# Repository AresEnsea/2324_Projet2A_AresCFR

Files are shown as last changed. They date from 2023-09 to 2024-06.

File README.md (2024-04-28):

# 2324_Projet2A_AresCFR
## Introduction

Ce repository GitHub regroupe l'ensemble des projets & documents réalisés par l'association Ares pour la Coupe de France de Robotique 2024.

## 26/09/2023: Idées pour résoudre le problème mécanique 
### I. Partie mécanique : 

Des recherches sur internet nous on fait découvrir le Robot Trooper. 
Le site suivant permet de connaître ce robot : https://www.sick.com/fr/fr/sick-sensor-blog/trooper-le-robot-de-manutention-autonome-pour-le-distancage-en-horticulture-/w/blog-instar-robotics-success-story/

Ce deuxième site permet d'étudier la mécanique de celui-ci grâce à un concours CPGE : https://www.upsti.fr/espace-etudiants/annales-de-concours/topics/s2i-robot-trooper

Les méthodes utilisées par le robot Trooper sont:

* La récupération de pots et de cache-pots grâce à des “mains plates”. 
* Le stockage des pots grâce à un arc de cercle.

<center>

My Remote Image

Figure 1 - Robot Trooper

</center>

## 03/10/2023: 
### II. Utilisation de capteurs de fin de course :

Idées : Positionner un capteur sur chaque côté du robot afin que le contact avec une des parois de la table permette de réinitialiser l'odométrie du robot. Par dessus, positionner une pièce imprimée en 3D pour couvrir la surface totale de chaque côté à l'instar des robots aspirateurs.  

<center>

aspirateur_robotique

Figure 2 - Robot Asprirateur

</center>

### III. Utilisation de capteurs TOF [Time Of Flight] :

La différence entre un capteur classique et un capteur TOF est l'état actif et passif. Le capteur classique est passif, il se comporte "comme la rétine d'un oeil". Cependant, un capteur TOF est un composant actif car il mesure un genre "d'écho" de la lumière qu'il émet (il ne mesure donc pas la lumière ambiante).
Le principe de fonctionnement de ce capteur est de mesurer le temps que met la lumière à revenir au capteur. Cela permet notamment de déterminer sa distance par rapport aux objets environnants. 

<center>



Figure 3 - Capteur TOF : Fonctionnement 
</center>

### IV. Idées de résolution du problème mécanique :

<center>

385482582_334418605664017_5041229388081065512_n

Figure 4 - Schéma explicatif de la solution mécanique 

</center>

<center>



Figure 5 - Modélisation 3D des pots à soulever (présence d'une bordure au sommet du pot) 

</center>

<center>



Figure 6 - Modélisation 3D des plantes à soulever (ne présente pas de bordure)

</center>

1) La base du robot : en forme d'entonnoir pour guider les plantes et leurs pots jusqu'à l'endroit où se situe la première pince.
2) Un ascensceur à pots : À l'endroit où l'entonnoir a le plus petit diamètre, une première pince se charge de monter les pots dans l'esapace de stockage.
3) Un espace de stockage intégré au robot : une plateforme comporte plusieurs encoches afin d'accueillir les pots.
4) Différenciation entre les pots et les plantes fragiles et résistantes : Utilisation d'un capteur de couleur pour détecter la couleur des plantes et ainsi déterminer s'il s'agit d'une plante fragile ou non. Pour détecter si le contenant stocké est un pot ou une plante, 2 capteurs de proximité seront placées à 2 hauteurs différentes : le capteur en position haute détectera les plantes et celui du bas les pots. Nous voudrions donc utiliser un capteur RFID (RFID-RC522) en haut de l'ascenseur pour savoir si c'est un pot ou une plante qui est monté par la pince. Il faut donc récupérer en premier des pots pour les stocker puis récupérer des plantes afin de les poser directement dans les pots.
5) Descente des pots contenant les plantes : Une deuxième pince est située à l'arrière du robot, elle est composée de deux plaques qui se serrent autour du pot afin de les descendre de l'espace de stockage et de les déposer sur la table. 

### IV. Servomoteur ou moteur :

Les servomoteurs respectent avec précision une position angulaire donnée. Ils ont une rotation souvent limitée à 180° et ne tournent pas en permanence alors qu'à l'inverse, les moteurs ont un mouvement continu. Les servomoteurs seront donc très utiles pour le déplacement d'un bras robotisé.

## 10/10/2023

### V. Décisions liées à la partie mécanique:

 - Dans les 6 zones de stockage deux caches-pots sont empilés. Puisque nous ne savons pas si le cache-pot sera en métal ou en impression 3D, nous choisisons de palier ce problème en adoptant la méthode suivante : dépose d'une plante dans les deux caches-pots empilés et placement dans les jardinières (comptera pour 1 point).
   
 - Première idée de stratégie pour ramasser les pots : Notre but est de récupérer des caches-pots et d'en avoir toujours en stock. Nous voulons ensuite mettre les plantes dans les caches-pots déjà stockés. Par ailleurs, si nous n'avons plus la possibilité de récupérer des caches-pots alors quelques emplacements auront un diamètre adapté à ceux des plantes fragiles. Lorsqu'il n'y aura plus de caches-pots à récupérer, nous utiliserons un capteur de couleur pour détecter si le robot prend une plante fragile ou une plante résitsante. Si la plantes est résistante alors la base du robot la poussera jusqu'à la zone de dépose des plantes. Si la plante est fragile alors elle sera stocké dans les emplacements adaptés situés dans le stockage avant de les déposer dans les jardinières.
   
 - Idée finale de stratégie pour ramasser les pots: Chaque cache-pot et chaque plante, de n'importe quel type, sera ramassé par la pince liée à l'ascenseur. Le système vérifiera quel type d'objet est encerclé par la pince. Pour chaque montée d'objet, un capteur détermine si c'est un cache-pot ou une plante (résistante ou fragile). Si c'est un cache-pot, alors il est dircetement déposé dans l'espace de stockage s'il reste un emplacement vide. Si c'est une plante fragile, alors elle est déposée dans un emplacement qui contient déjà un pot. Si c'est une plante résistante, alors elle est déposée dans un emplacement vide si c'est possible, sinon elle est déposée dans un emplacement contenant un pot.
   
 - Résolution de l'éclairement des panneaux solaires: Positionnement de deux crémaillères sur le côté du robot afin d'appuyer sur le côté du panneau solaire pour le faire tourner d'un quart de tour.
   
 -  Dépot des plantes avec leurs caches-pots dans les jardinières : Une pince est située à l'arrière du robot. À l'endroit où les pots peuvent sortir de l'espace de stockage, nous plaçons une plaque en bois posée sur des rails qui avance et recule selon une direction. Les dimensions de la plaque en bois sont : $75mm \times 75mm \times 6mm$. De plus, nous plaçons une pince à 75 mm de distance de l'espace de stockage. Celle-ci va pouvoir récupérer les pots grâce à la plaque de bois qui avance.

## 17/10/2023

### VI. Informations concernant les actionneurs 

#### VI.a Servomoteur Dynamixel AX-12 :

<center>

Dimension_AX12

</center>

Caractéristiques:
- Tension de fonctionnement: 9 à 12V
- Couple décrochage (N.m) : 1,52 à 12V et 1,5A
- Vitesse hors-charge: 59 tours/minute
- Vitesse: 0,196 s/60° (à 10 Vcc)
- Température opérationnelle: -5°C à 70°C
- Vitesse de communication: 7343 bps à 1 Mbps
- Compatible avec AX-12+ à l'échelle 1:1
- Rapport de réduction: 254:1
- Poids : 54,6g
- Dimensions (mm) : 32 x 50,1 x 40

Détails :
- Fonctionnement en rotation continue ou de 0 à 300°.
- Le contrôleur de ce servomoteur permet un retour d'information de la position, de la température, du couple et de la tension d'alimentation.
- Les moteurs disposent de deux connecteurs 3 broches (cordon inclus) permettant de relier plusieurs moteurs en cascade et de les utiliser ensemble.
- Vérification de la mise à zéro grâce à deux encoches.
- Idée de code : CDR2022_23/2A/Project__Ax12/Core/main

#### VI.b Mirco Servomoteur MG90S :

<center>

MG

</center>

Caractéristiques :
- Tension : 4,8 V - 6,0 V
- Vitesse : 0,10 s / 60 degrés
- Couple : 1,8 kg/cm (4,8 V)
- Température : -30 à +60
- Bande passante morte : 5usec

#### I.b Servomoteur SG90 :

<center>

servomoteursg90
dimension_sg90

</center>

– Dimensions : 22 x 11.5 x 27 mm
– Poids : 9 g
– Tension d’alimentation : 4.8V à 6V
– Vitesse : 0.12 s / 60° sous 4.8V
– Couple : 1.2 Kg / cm sous 4.8V
– Amplitude : de 0° à 180°

Correspondance des fils de la prise de type Graupner à 3 fils :
Marron -> GND
Rouge -> 5V
Orange -> Commande PWM

Détails : exemple de code ARDU*** : https://robotix.ah-oui.org/user_docs/dos10/sg90-datasheet.pdf

## Pendant les vacances de Novembre :

Nous nous sommes focalisés sur la mécanique du projet afin d'avoir une vision globale du robot et de ses composants que nous devrons par la suite commander.
La dernière grosse partie mécanique a concevoir est la pince avant du robot qui servira à attraper les pots et à les déposer sur la table ou dans les jardinières. Celle-ci a été réalisée grâce au logiciel fusion. 

#### Première version de la pince :
<center>

Pince_v1

</center>

#### Deuxième version de la pince :

<center>

Pince_v2

</center>

## 12/11/2023 :

Première version de la CAO et de l'assemblage de l'ensemble des pièces du robot (Utilisation avec modifications de certaines pièces des années précédentes et modélisation de nouvelles pièces).

Assemblage du robot : cette première version ne prend pas en compte la pince arrière car nous souhaitons d'abord être certain d'arriver à construire complètement une pince entièrement. Nous la dupliquerons par la suite pour la mettre à l'arrière du robot. 

#### Changement de l'attache de la pince à l'ascenseur :  

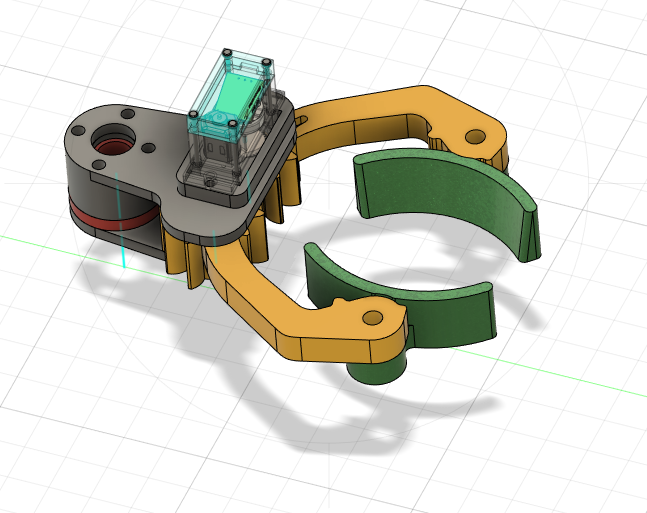
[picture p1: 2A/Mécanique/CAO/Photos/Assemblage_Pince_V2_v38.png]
Assemblage_Pince_V2 v38


Création de pièces et assemblage de celles-ci avec des pièces utilisées les années passées (ex: roues/batteries/équerres) pour concevoir le robot entièrement :

<center>



</center>

## 27/11/2023:

- Finalisation de la première version de toutes les pièces du robot
- Impression de toutes les pièces afin de les tester 

## Décembre 2023:

- Modification du bord de soutien des pots. Utilisation d'une imprimante avec un plus grand plateau afin que la pièce soit imprimée en une fois pour ne pas avoir besoin de la découper en plusieurs parties. Nous avons également augmenter la hauteur de ce bord afin que la plaque en bois soit bien contrainte à rester au milieu de la pièce. Conception de pylônes de soutien. 

- Les tests de ce bord de soutien nous ont incité à agrandir son ouverture afin de laisser plus de place aux pots lors de leur sortie.  

- Création de la pièce utilisée pour faire sortir les pots de l'espace de stockage. La modification à apporter est la modification de la forme de celle-ci afin qu'elle soit identique à la forme des pots pour qu'elle soit correctement ajustée à ces derniers.  
- Nous avons également ajouté les inserts et les vis dans chaque conception afin de monter le robot entièrement.  
- Les actionneurs AX12 ont été remplacés par des petits servomoteurs SG90 pour leur taille et leur facilité de commande.

### Améliorations à réaliser:  

- Les bords du stockage sont un peu haut et certaines plantes peuvent se coincer en passant sous le stockage. La modification à apporter est sur la hauteur des piliers de soutien.
- Décaler la position de l'ascenseur pour laisser plus de place à la rotation des pots.
- Augmenter la taille de l'ascenseur pour éviter la collision entre les pots.
- Les roues ne touchent pas le sol, il faudrat donc modifier la pièce de maintien des moteurs pas à pas (correction des trous pour l'odométrie).

## Janvier 2023: 

### CAO

- Changement des actionneurs SG90 par des XL-320 pour des raisons de performance et de connectivité simplifiée.  
- L'ascenseur a été amélioré pour faciliter la rotation de la pince et a été rehaussé pour limiter la perte de pots potentiels.  
- La pince a été améliorée pour recevoir un XL-320.
- Le pousse-pot a été amélioré pour recevoir un XL-320.
- Le périmètre du robot à été réduit.

### Électronique

- Réalisation du schématique et du PCB de la carte mère du robot.
- Choix de différents capteurs de détection de pots (capteur de couleurs et de proximité).

#### Réalisation du schéma Électronique  
On commence par réaliser le schéma fonctionnel pour avoir une petite idée de l'architecture de la carte principale du robot: 

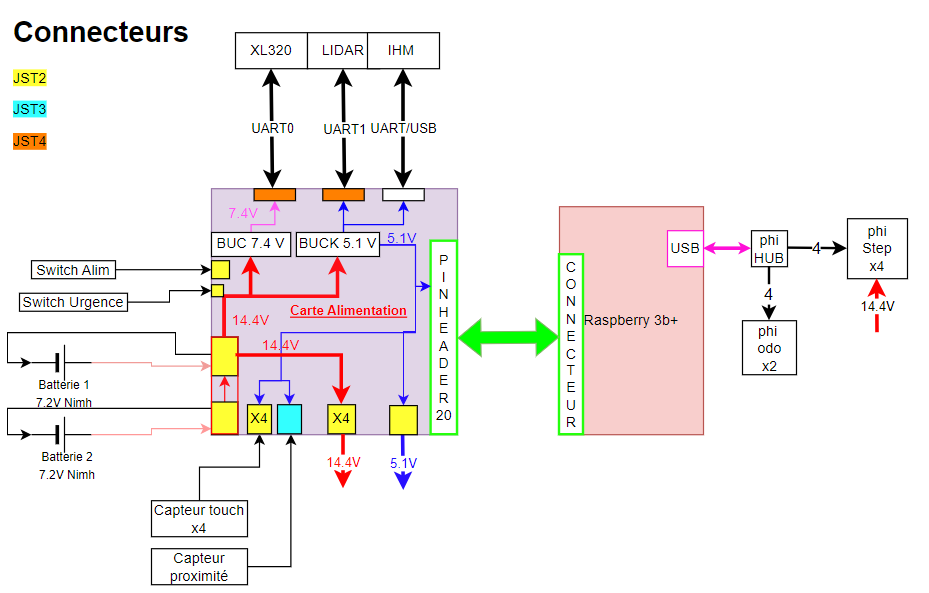
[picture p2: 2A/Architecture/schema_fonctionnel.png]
Schéma fonctionnel
  

On réalise ensuite le schéma électronique avec les composants de base tout en ajoutant les composants inexistants .
Pour faciliter la lisibilité des différentes parties du schéma (conversion, communication ou encore calcul ), nous les séparons dans des blocs ou des sous-pages.

##### Partie alimentation de la carte :  

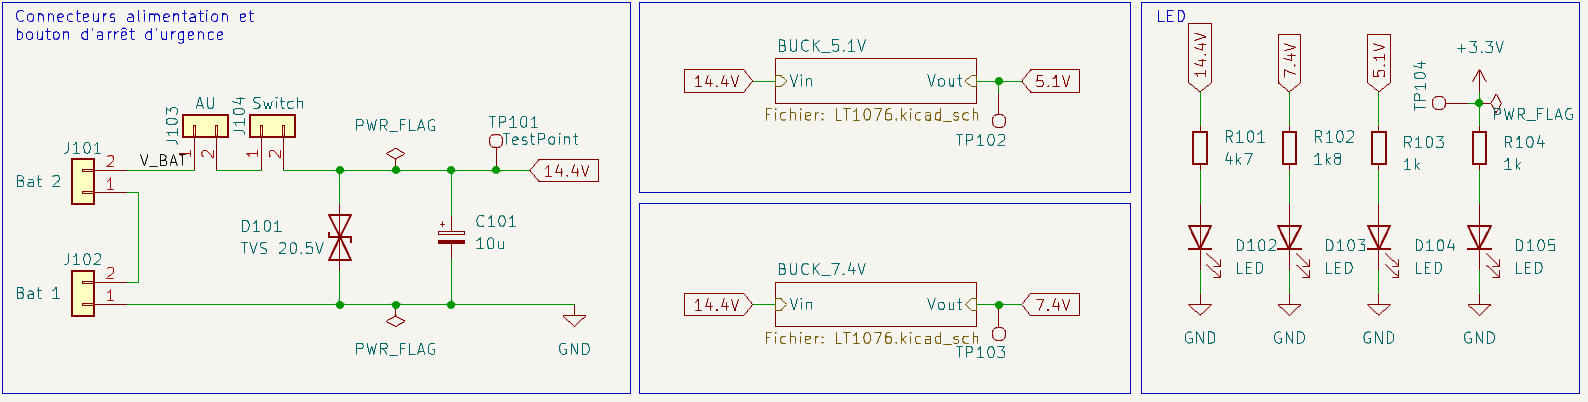
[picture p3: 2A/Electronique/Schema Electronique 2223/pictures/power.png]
Power
  

Pour cette partie nous avons repris certaines idées du schématique réalisé pour la Coupe de France de Robotique 2023 (notamment pour la partie qui concerne la batterie et le bouton d'arrêt d'urgence).
La taille du PCB a été choisie de manière à ce qu'elle puisse s'empiler avec une Raspberry Pi 4. 

De plus, nous avons du faire attention à la présence de détrompeurs sur les connecteurs et nous avons donc décidé de retirer le système anti-inversion de polarité et anti-retour de courant. De même pour le fusible de protection car il n'a jamais servi auparavant.
Nous avons par ailleurs choisi de conserver la diode TES pour les surtensions ainsi que le condensateur de filtrage.  

Comme nous l'avons décrit dans le schéma fonctionnel, nous avons besoin des tensions suivantes: 5.1V, 7.4V ainsi que du 3.3V pour les différents actionneurs. Nous allons donc devoir utiliser des convertisseurs Bucks car les 2 batteries branchées en série fournissent du 14.4V.

Remarque: Lorsque deux schémas sont similaires, afin de rendre plus lisible le schématique, nous créons des pages hiérarchiques sur lesquelles seuls les entrées et sorties apparaissent sur la page principale :

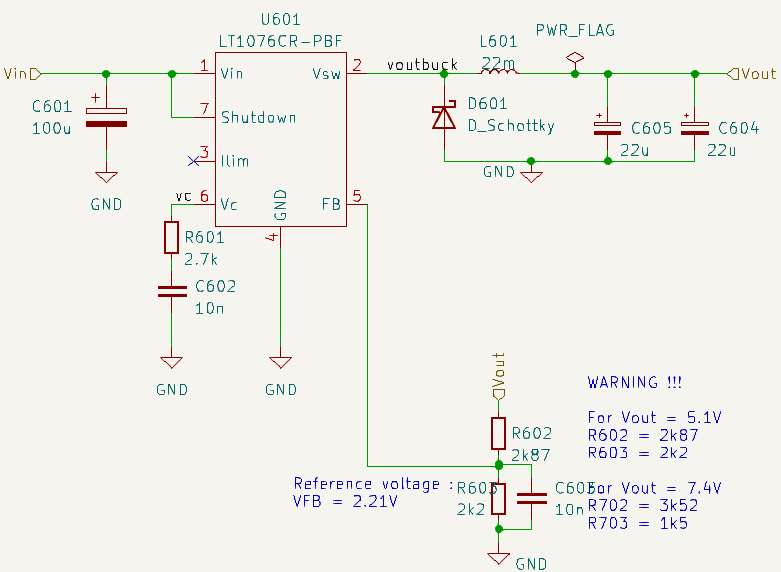
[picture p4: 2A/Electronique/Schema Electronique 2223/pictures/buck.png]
Buck
  

Dans ce buck, nous devons faire attention aux valeurs des résistances du pont diviseur de tension afin de délivrer la tension souhaitée [5.1V ou 7.4V].

/!\ C'est là qu'intervient la limite de l'utilisation de la page hiérarchique, car les deux bucks doivent avoir des valeurs de résitances différentes (nous n'avons pas trouvé de solution pour résoudre ce problème dans les pages hiérarchiques, bien que la solution doit exister sur des forums).  

Nous avons également choisi de mettre 2 capacités de 22uF en parrallèles afin d'avoir plus de facilités pour le soudage des composants sur le PCB (c'est également pour améliorer la qualité du routage).

La référence du pont diviseur aurait dû idéalement être mis au GND du buck pour être au plus proche afin de calculer la différence de tension et réguler la tension le mieux possible. 
Une fois les alimentations mises en place, nous rajoutons des LEDs de contrôle sur chaque tension afin de surveiller visuellement l'état des tensions. Nous rajoutons également des points de tests afin de controler les tensions avec un voltmètre.  

Nous avons par la suite réalisé la partie qui concerne les capteurs avec les différents types de communication :

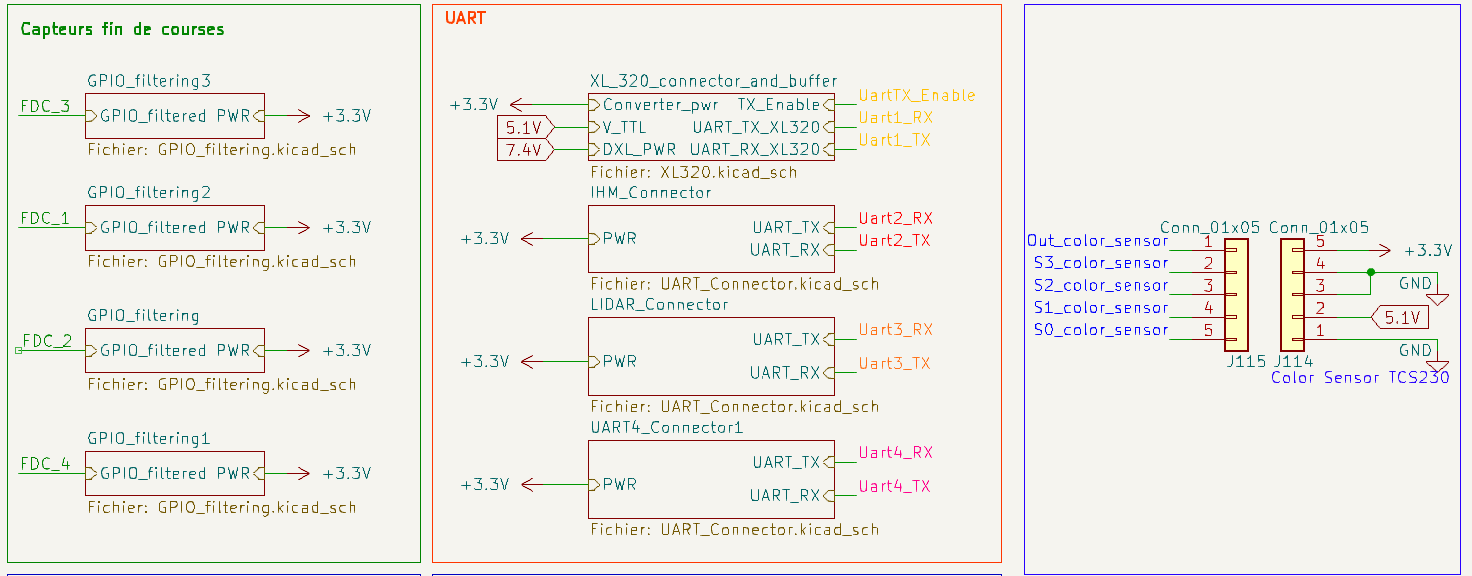
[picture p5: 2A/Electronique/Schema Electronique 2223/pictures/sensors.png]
sensors


Les capteurs font appels à des communications séries UART et des GPIO pour le capteur de couleur et les capteurs fin de course.  

#### Capteurs Fin de course:  

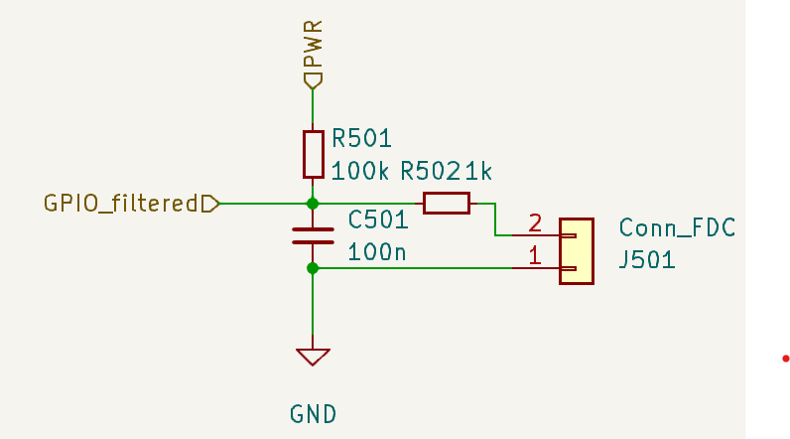
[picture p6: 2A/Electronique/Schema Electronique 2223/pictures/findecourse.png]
Capteur fin de course
  

Lorsque nous appuyons sur un bouton et que nous le relâchons, un effet rebond apparaît : le microcontrolleur perçoit" plusieurs appuis/relâchements rapides.  
Pour limiter ce défaut, nous ajoutons un filtre RC qui a un objetcif de lissage. Nous ajoutons également une résistance de tirage pour éviter l'effet antenne lorsque le bouton est ouvert.  

#### UART:  

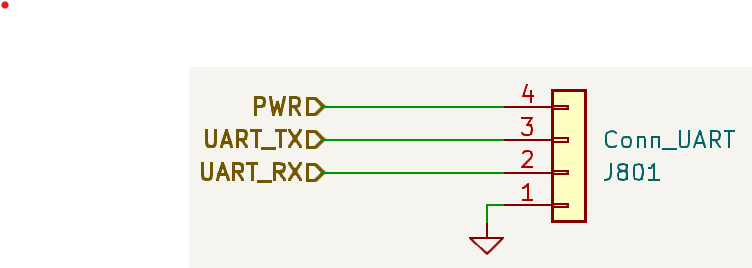
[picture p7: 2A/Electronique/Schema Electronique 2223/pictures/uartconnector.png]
UART
  

Contrairement aux années précédentes nous avons décidé d'enlever les diodes TVS anti-surtension par manque de place.  

#### Connection XL-320: 

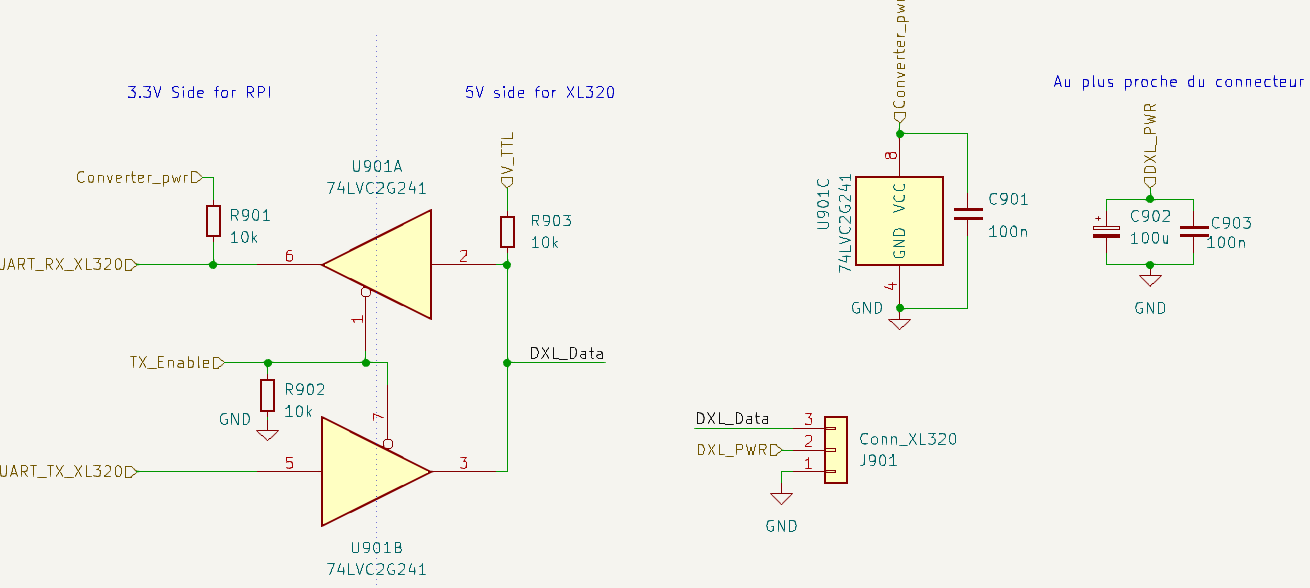
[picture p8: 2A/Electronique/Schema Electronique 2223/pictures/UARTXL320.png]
uartxl320
  

Pour le contrôle des XL-320, le protocole fait appel à une connexion série UART half-duplex (communication dans un sens à la fois) en 5V, or la Raspberry Pi 4 utilise des UARTs full-duplex en 3.3V.

Nous utilisons donc le 74LVC2G241 pour convertir du half en full duplex (communication dans les deux sens en même temps). De plus, ce module permet de remplacer un level shifter pour adapter la tension de communication.  

#### Capteurs de couleur:
Le capteur de couleur fonctionne en 5V mais également en 3.3V, ce qui est intéréssant pour notre Raspberry qui n'accepte qu'uniquement du 3.3V.

Nous relions tous les signaux à la Raspberry (nous l'avons choisie afin d'avoir 4 UART à disposition) et nous récupèrons le 3.3V pour l'alimentation 3v3.

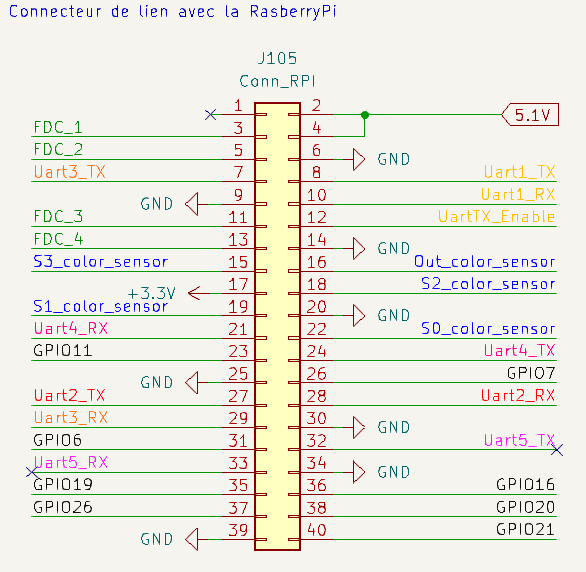
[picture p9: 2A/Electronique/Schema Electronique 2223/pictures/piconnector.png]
connecteur
  

On finit par rajouter les GPIO non utilisés de la pi sur un bornier avec l'alimentation à coté pour pouvoir rajouter de potentiels capteurs supplémentaires.  

On lance le contrôle de règles électrique, on ajuste le schématique afin de corriger les erreurs et nous obetnons ce magnifique schéma :

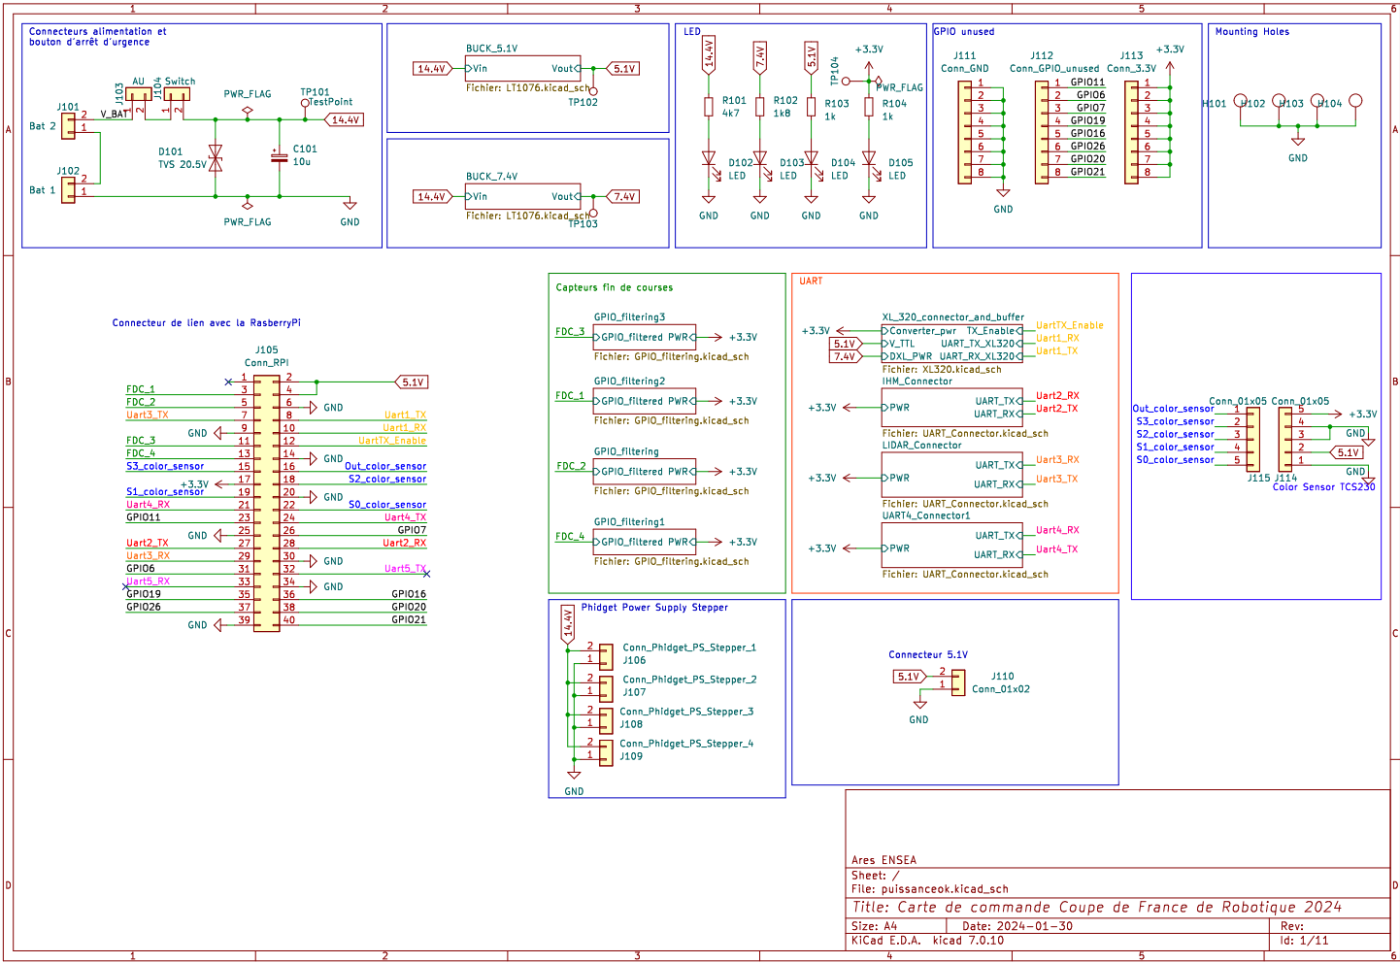
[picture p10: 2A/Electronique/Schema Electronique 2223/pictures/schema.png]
schema final
  

(Ne pas oublier de bien référencer tous les composants hormis les small capacités, résistances et LEDs).

#### Réalisation du PCB 4 couches  
##### 1ère étape :

Il faut commencer par affecter les bonnes empreintes aux composants et les créer si elles n'existent pas.
Par exemple, tous les connecteurs JST sont référencés, cependant pour l'allimentation principale nous avons décidé de prendre des connecteurs plus gros et qui ne sont pas référencés.  

##### 2ème étape :  

On place les composants sur notre PCB en pensant à bien prendre en compte la proximité des composants (condensateurs de filtrage, résistances, ...) avec les signaux concernés et de regrouper les alimentations.  

Cela nous a "obligé" à séparer une grosse capacité en 2 petites.
Dans notre cas, la place était assez restreinte car nous ne pouvions pas mettre de condensateurs sous la carte pour éviter de percuter les composants qui se situent déjà sur la PI4.
Dans ce cas, le chevauchement de sérigraphie n'est alors plus un problème.

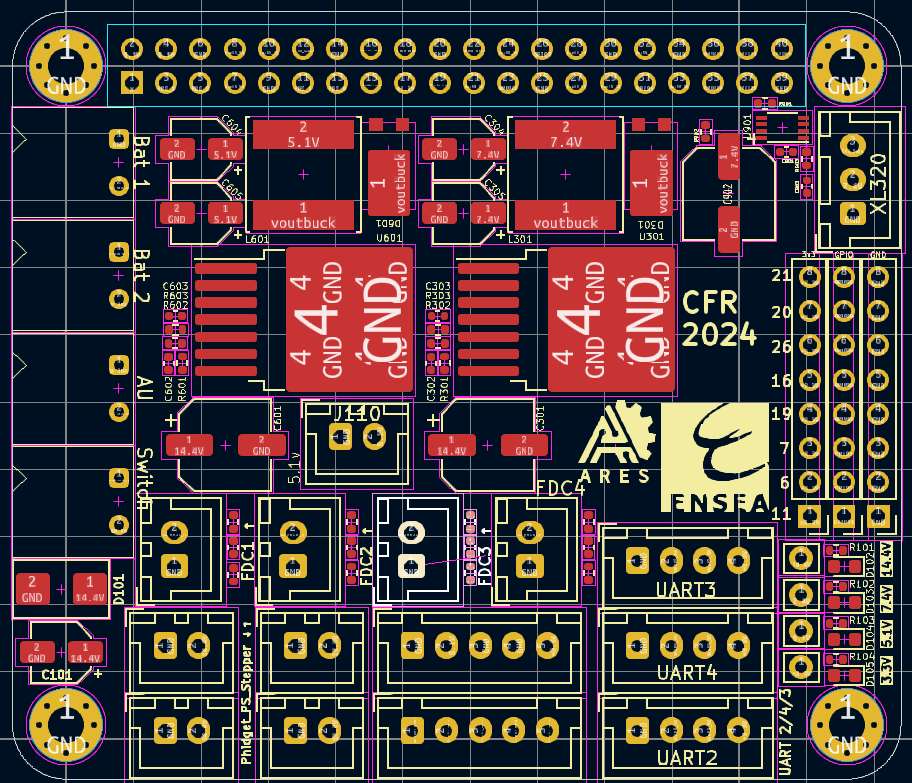
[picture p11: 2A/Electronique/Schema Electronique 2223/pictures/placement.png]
Placement
  

##### 3ème étape :

Nous devons régler différents paramètres pour définir une taille de piste et de via en fonction du courant qui passera à travers (notamment en utilisant le calculateur de kicad), ainsi que l'isolation en fonction de la tension.

On commence par placer les plans de masse et d'alimentation en fonction du placements des composants.  
Dans notre cas, nous avons choisis de faire la première couche signal/alimentation/composants/masse, deuxième plan de masse dans lequel nous nous interdisons le placement de pistes pour la laisser la plus intacte possible, et le troisième plan de puissance dans lequel nous créeons des zones 3.3v , 5.1v , 7.4v et 14.4v afin de faciliter le routage.
Nous terminons par la dernière couche qui est aussi un couche de signal/masse.

Dans l'idéal, il faudrait réaliser une cage de Faraday en mettant le plan d'allimentation et le plan de masse de part et d'autre du plan de signal. Cepandant, cela empêche toute intervention de rectification de routage après fabrication (en cas de problème).  
Nous débutons la réalisation du routage des alimentations en veillant à bien faire des grosses pistes, plusieurs vias ou bien des zones.

Enfin, nous réalisons le routage des signaux en faisant des bus de pistes pour améliorer la propreté et nous modifions le schéma lorsque c'est nécéssaire pour le "faciliter".

/!\ Éviter les pistes trop longues qui font le tour du pcb !

Il faut par la suite lancer l'analyse des règles électriques ainsi que rectifier les différents problèmes.
Nous obtenons, principalement grâce à l'aide de Monsieur Papazoglou le magnifique PCB suivant : 

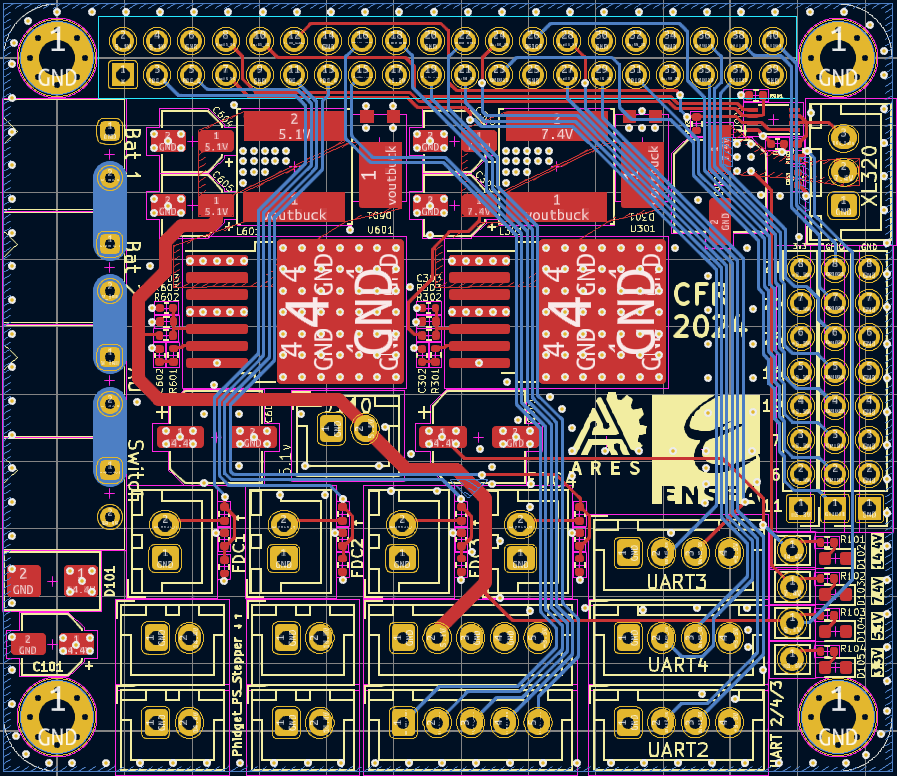
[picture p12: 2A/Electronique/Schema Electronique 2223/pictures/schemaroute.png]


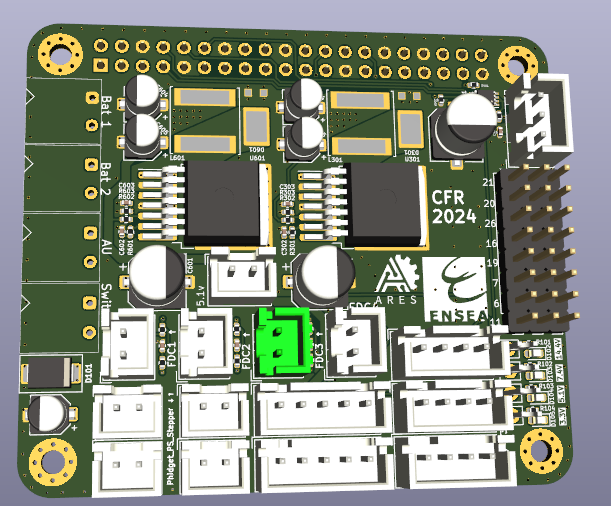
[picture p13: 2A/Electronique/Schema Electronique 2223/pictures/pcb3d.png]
  

### Code  

- Test du capteur de couleurs : Les essais réalisés avec le capteur de couleur se sont révélés assez satisfaisants pour distinguer les pots blancs des pots violets, mais cela ne permet pas de différencier les pots blancs des pots métalliques. Pour pallier ce problème, nous combinons l'utilisation du capteur avec celui d'un capteur à induction, ce dernier permettant de détecter les objets métalliques à sa proximité.

### Brasage (Soudure)  

Notre carte PCB de puissance 3 couches a été commandée en 5 exemplaires.

Tout d'abord, nous avons choisi de souder entièrement une carte électronique afin de vérifier son fonctionnement global. 

Les étapes de la soudure des composants grâce au four sont :

- Le placement de la carte à souder entre 4 autres cartes avec du scotch autour afin que la carte principale ne bouge pas.
- Le chauffage de la pâte à braser entre les mains.
- L'étalage de la pâte sur le PCB grâce à une carte en plastique.
- La pose des boîtiers des composants de différentes tailles sur la paillasse.
- L'affichage du schématique et du routage KiCad afin de suivre les valeurs des composants.
- Le positionnement de tous les composants sur le PCB
- La vérification que chaque composant est correctement positionné et n'a pas bougé.
- L'allumage du four, l'attente du préchauffage puis le placement de la carte électornique à l'intérieur.
- Le suivi de l'évolution de la cuisson via l'ordinateur de suivi (augmentation de la température, arrivée au point culminant, baisse de la température).

Remarque importante : Il faut commencer par positionner les composants sur la carte par ordre de taille croissante.

Par la suite, une fois que tous les composants CMS ont été soudés, il faut vérifier si les tensions qui sortent de la carte ont la bonne valeur. Pour ce faire, on utilise une alimentation et un voltmètre aux bornes des points de test. Si toutes les valeurs recuillies sont cohérentes avec celles attendues, alors nous pouvons passer à l'étape suivante. Sinon, il faut faire des réajustements sur la source du problème (composants, soudure, ...).

Puis, il faut ajouter les composants traversants (connecteurs des batteries, du bouton d'arrêt d'urgence, des capteurs et des actionneurs, ...).
Pour ce faire, il faut utiliser une pince afin de tenir la carte en hauteur afin de pouvoir souder correctement les différents composants qui ont des tailles différentes.

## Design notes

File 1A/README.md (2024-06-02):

# Coupe de France de Robotique 2024 : les PAMI
> A l'occasion de la Coupe de France de Robotique 2024 : "Farming Mars", nous avons décidé de créer plusieurs PAMI (Petits Automatates Motorisés indépedants) qui devront réaliser des actions simples afin de rapporter des points à l'équipe de l'ENSEA  en assistant le robot principal. Ces PAMI doivent pouvoir se déplacer sur le plateau de la Coupe et être en mesure de détécter les robots adverses pour être homologués 

# Equipe
> L'équipe PAMI est composé de 4 élèves de 1ère année : <br>
> -Antoine Lemarignier <br>
> -Ewan Zarha Thenault <br>
> -Nathan Bainard <br>
> -Mateo Gomes <br>

# Journal de bord
>-Déroulé séance par séance

## Séance 1
>-installation machine virtuelle Ubuntu + début configuration Pi4 <br>
>-dessin du PAMI <br>
>-verification fonctionnement lidar <br>
>-utilisation github (push/pull/clone) <br>

## Séance 2
>-creation organigramme <br>
>-suite configuration machine virtuelle (configuration réseau à continuer en dehors de la séance) <br>
>-code écran (vérification) <br>
>-recherche modules récepteur émeteur 433mHz <br>

## Séance 3
>-changements schématique <br>
>-vérification moteur : fonctionnement partiel <br>

## Séance 4
>-1ère version routage <br>
>-vérification moteur : incomplet <br>

## Séance 5
>-nouvelle version pcb <br>
>-bon fonctionnement moteurs après changement de driver <br>
>-début écriture du code moteur <br>

## Séance 6
>-pcb : soudage des composants <br>

## Séance 7
>-fin soudage composants et test avec moteurs (les pcb marchent bien) <br>

## Séance 8
>-Code final qui doit fusionner le code du Lidar des roues et de l'écran <br>
>-Méca : Impression des deux autres modèles 3D pour les autres pamis <br>

## Séance 9
Après Coupe :
>-Vision : essai concluant avec tag aruco <br>
>-Complément Githhub <br>

## Séance 10
>-Derniers essais avant démonstration <br>

# Livrables
## PCB
> Présentation du schéma (grandes lignes) + PCB



## Code
> Architecture du code
> 

## Getting Started Guide
> Ici le manuel d'utilisation simple et pratique ! <br>
> Le pami fonctionne de la manière suivante : après démarrage avec le switch (allume les leds rouges),
vérifier qu'une tirette (ou un pont) est bien positionnée sur les deux pins du connecteur J102,  appuyer sur le SW NRST pour initialiser l'écran, une fois fait, le BTN2 permet de changer de stratégie parmi celles définies dans "strategy.c" dans le projet STM32CubeIDE, enfin pour démarrer le pami simplement enlever la tirette (ce qui aura pour effet de démarrer le robot après un délai de 90s ou bien appuyer sur le bouton du millieu (BTN1) pour le démarrer immédiatement.

## Rendu final
>Video ici de votre projet :
> - https://github.com/AresEnsea/2324_Projet2A_AresCFR/assets/88663397/23594f17-0ef2-46ef-a65a-15afedc95028
> - https://github.com/AresEnsea/2324_Projet2A_AresCFR/assets/88663397/61659872-7cb5-43fb-a910-f1500b88333c

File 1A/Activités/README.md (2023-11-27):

# Activités
Ce dossier regroupe deux livrets rédigés par Ousmane THIONGANE. L'un permet de découvrir la programmation avec Mbed, et l'autre le routage avec KiCad. Il peuvent être réutilisés au fil des années pour réaliser des activités de rentrée, ou simplement pour s'exercer à l'électronique et l'informatique.

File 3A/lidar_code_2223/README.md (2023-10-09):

# LIDAR Ares v1.4

Ce programme a televerser sur le MCU du LIDAR STM32G070 permet 
d'utiliser 16 capteurs infrarouges VL53L1X pour mesurer la distance qui separe le robot des obstacles.
Les mesures et la position du capteur correspondant sont envoyees en serie a la carte de strategie du robot,
en ayant filtre les distances trop importantes.

Caracteristiques :
- Rafraichissement maximum toutes les 50ms
- 13 ROIs (1 different a chaque tournee de mesures)
- 16 Capteurs
- Communication serie a 115200 kHz
- Distance fiable entre 10cm et 1m
- Les LEDs au dessus des capteurs deconnectes clignottent a la frequence de rafraichessement

Trame :
Header 		-> Nbre de capteurs actifs
			-> Nbre de ROIs utilises
			-> Nbre de mesures envoyees
			
Contenu		-> N°capteur*NbreROIs + N°ROI + 1
			-> Distance sur 16bits (poids forts)
			-> Distance sur 16bits (poids faibles)
			
Delimiteurs -> 0xFF, 0xFF, 0xFF (debut et fin)

Pistes d'amelioration :
- Supprimer les ROIs ou en mettre seulement 2 pour obtenir une resolution de 1/32 
avec un taux de rafraichissement encore acceptable
- Regler les distances d'offset de chaque capteur (actuellement ~+5cm)
- Ajouter la possiblite pour la carte de strategie de parametrer la distance maximale d'envoi des mesures,
ou le nombre de ROIs, ou de redemarrer le lidar,
en passant par la communication serie.

Note :
- En raison du nombre de capteurs mis en parallele il faut que les levels shifters et regulateurs 
des VL53L1X soient retire sinon au dela de 8 capteurs les capteurs n'arrivent plus a repondre au MCU.

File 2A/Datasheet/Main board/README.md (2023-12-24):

# Inventaire de la carte mère

## Intelligence
- Carte Nucleo F446RE
- LED R971 (2pcs)
- Resistance (10 pcs)
  - 100 ohms
  - 1k (9pcs)
- Diode DF3A6 (6pcs)
  
## Motorisation
- transistor PMOS 70327
- transistor MBT3906DW1
- resistance 10k (2pcs)
- Driver drv8825 (2pcs)
- Condensateur 100uF
  
## Odometrie
- Resistance 4k (4pcs)
- encoder
## Alimentation
- Fusible
  - 10A
  - 15A
- Resistance (2pcs)
  - 680ohm
  - 10k
- LED LG_R971
- Convertisseur DC/DC TSR124540
- PMOS S4985
- SM6T24A

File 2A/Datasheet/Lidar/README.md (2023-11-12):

# Inventaire de lidar

## Alimentation
- Ampli buck 3v3 "datasheet à rajouter"
- PMOS		       "datasheet à rajouter"
- Diode transil	SM6T6V8A
- Diode zener	CD0603
- polyfuse	     "datasheet à rajouter"
- resistance 	10k
- condensateur  22u/10u

## Capteur
- TOF  VL53L1      (16 pcs)
- resistance   10k (32 pcs)
- condensateur 1uF (16 pcs)

## MCU
- STM32G070
- quarz 16MHz "datasheet à rajouter"
- Condensateur 20p (2pcs)
- Condensateur 100n (2pcs)
- Condensateur 4.7uF
- NUP2105L
- resistance 2.2k (2pcs)
## LED
- Led (16pcs)
- resistance 3k (16pcs)

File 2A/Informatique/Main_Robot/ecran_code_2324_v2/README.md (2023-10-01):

# Présentation du projet
Globalement tout ce joue dans strategie.c, score.c et le dossier image.

Dans strategie.c il y a la création des boutons et leurs attribution de couleur, il y a plusieur couleur comme le jaune -> LV_PALETTE_YELLOW ou encore le bleu -> LV_PALETTE_BLUE
toute les couleur disponible sont dans un enum que vous pourrez trouver dans la librairie lv_style.h
Il est important de noter que la couleur noir dans lv_style.h est LV_PALETTE_NONE
une fois un bouton sélectionné et que vous appuyé sur "confirmer" un envoie série est réalisé vers la carte principale sous la forme de "%d \r\n".
le %d envoyer sera la valeur du bouton sélectionné

Pour changer l'image de fond il faut changer le code c de TableRedi.c, en gros vous prenez une image .png qui tiens sur l'écran de 480x272 et vous allez sur ce site :
https://lvgl.io/tools/imageconverter
Sur le site vous uplodé votre image préalablement nommé TableRedi.png, ce sera plus simple car en gardant le nom du .c vous pourrez simplement récupérer
le txt générer par le site et copier puis écraser le précédent code dans TableRedi.c . Le process est le même pour changer les chiffres du score et tout est
dans le dossier Image.

score.c justement, en fait il fonctionne avec une interruption sur le RX qui utilise un callback. Donc dés qu'il reçois un char correspondant à un chiffre il l'affichera.
Je me souviens plus trop mais il me semble que ça affiche ce que vous envoyé genre vous envoyé "10" en série ça affichera 10 sur le score

# LVGL ported to STM32F746 Discovery

This is LVGL ported to [STM32F746G-DISCO](https://www.st.com/en/evaluation-tools/32f746gdiscovery.html) using 
[CubeIDE](https://www.st.com/en/development-tools/stm32cubeide.html) or IAR Embedded Workbench.

## Try it with just a few clicks!

1. Download [lv_stm32f746.bin.zip](https://nightly.link/lvgl/lv_port_stm32f746_disco/workflows/stm32_port/master/lv_stm32f746.bin.zip) and extract the binary inside.
2. Plug in the Discovery board.
3. Copy the binary to the `DIS_F746NG` drive provided by the board's USB interface.



# How to compile and make changes
1. Clone (or download) this GitHub repository to a folder on your computer and update the submodules:
`git clone --recursive https://github.com/lvgl/lv_port_stm32f746_disco.git`
2. Open or import the project.
  * CubeIDE
    1. Install [CubeIDE](https://www.st.com/en/development-tools/stm32cubeide.html).
    2. Import the project into your workspace.
  * IAR Embedded Workbench

    * Open IAR workspace at `ide/iar/stm32f746_disco_lvgl.eww`

      **NOTE**: LVGL does **NOT** support the 'multi-file compilation' mode.
3. Connect the Discovery board
4. Build and run!

# How to build using VSCode and Devcontainers

## Prerequisits
* [Visual Studio Code](https://code.visualstudio.com/Download)
* [Visual Studio Code Extension : Remote - Containers](https://marketplace.visualstudio.com/items?itemName=ms-vscode-remote.remote-containers) 
* [Docker Desktop](https://docs.docker.com/desktop/)

## Using Devcontainers
For the background to Microsoft's Development containers see [here](https://code.visualstudio.com/docs/remote/containers)

At the project root, open the project using VSCode
```
$ code .
```

VSCode will then pop up a dialog:
```
Folder contains a Dev Container configuration file. Reopen folder to develop in a container
```
Select *Reopen in Container*

First time through this will build a Docker image from scratch using `.devcontainer/Dockerfile` - this may take a couple of minutes as it includes downloading the `gcc-arm-none-eabi` toolset from `developer.arm.com`. This build is a one-off operation.

Once VSCode has created the Docker image and launched the container, open a new Terminal window (using the VSCode menu). You are now working in an Ubuntu based envrionment.

## To Build

There is a build script supplied. Simply run
```
$ ./build.sh
```
This will create the artifacts:

* `build/debug/lv_stm32f746.elf` 
* `build/debug/lv_stm32f746.bin`

To rebuild, simple repeat:
```
$ ./build.sh
```

If you add new files, then run:
```
$ ./build.sh reset
```

## Debugging

To debug from within the container, `OpenOCD` need to run locally to connect to the target board.

In a terminal window run
```
openocd -f Release/stm32f7.cfg
```
OpenOCD will then wait on port `3333` for a gdb connection
```
Info : starting gdb server for stm32f7x.cpu on 3333
Info : Listening on port 3333 for gdb connections
```

In VSCode/devcontainer select the Run/Debug option `Debug (Remote OpenOCD)`. 

The container uses `arm-none-eabi-gdb` to connect to OpenOCD on port `3333` to reflash the board and support source-level debug.

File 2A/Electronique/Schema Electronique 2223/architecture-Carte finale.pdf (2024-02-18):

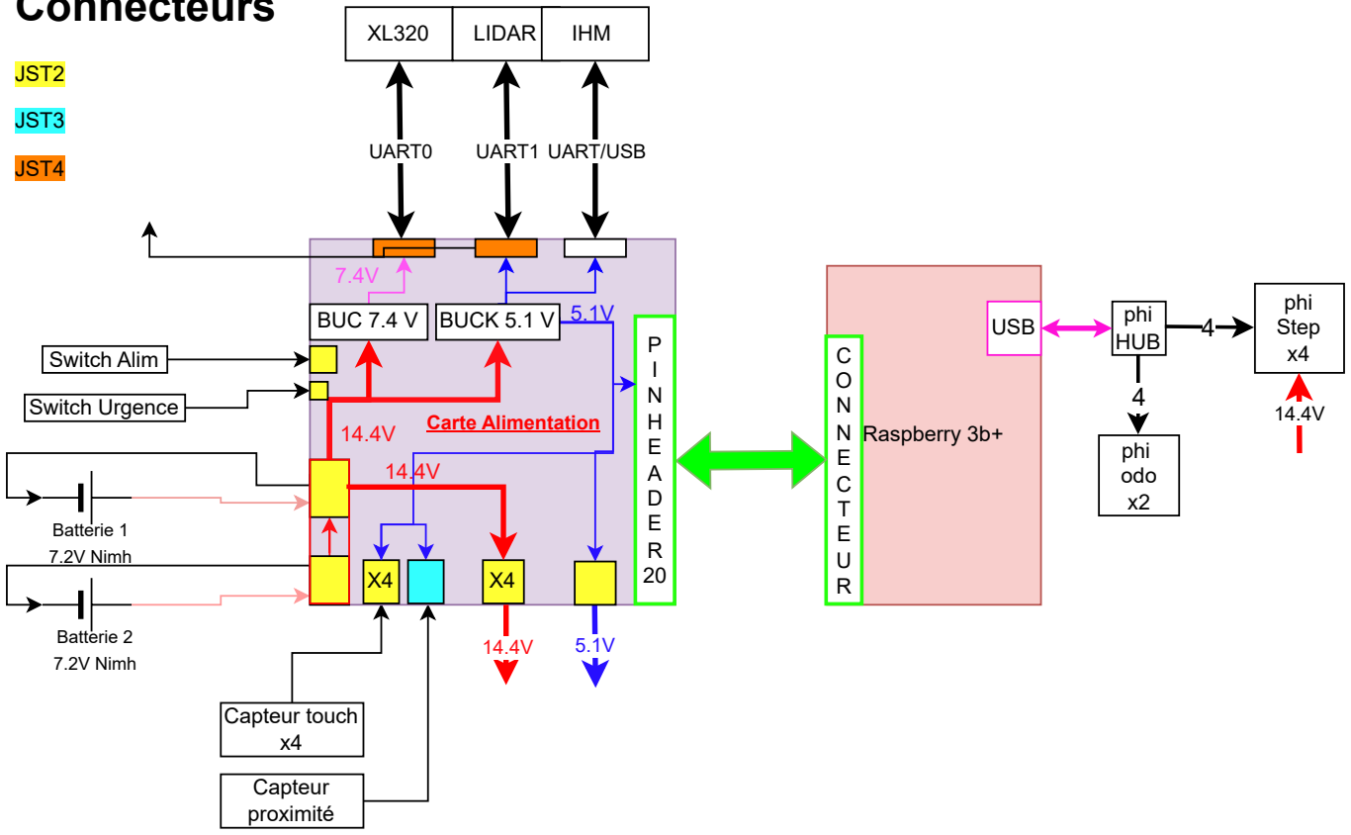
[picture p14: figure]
Raspberry 3b+; USB; phi HUB; phi Step x4; phi odo x2; Batterie 2 7.2V Nimh; Batterie 1 7.2V Nimh; UART0; LIDAR; UART1; IHM; UART/USB; Switch Alim; Switch Urgence; Capteur touch x4; Capteur proximité; Carte Alimentation; BUC 7.4 V BUCK 5.1 V; JST2; JST3; JST4

# Connecteurs

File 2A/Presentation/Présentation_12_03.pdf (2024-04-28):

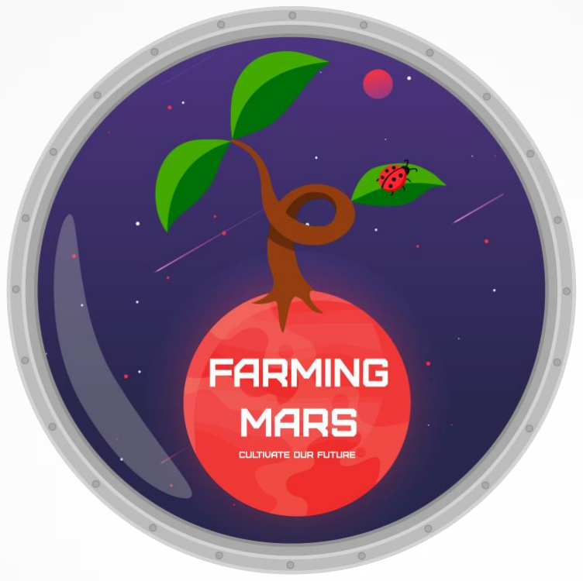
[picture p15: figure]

# Présentation de projet

## Coupe de France de Robotique

## - Avancement-

1

BICHEMIN Fannie
FAGET Nathan
THIONGANE Ousmane
WEIDLE Rémi

## Présentation de projet

### 12 Mars 2024

2

### Aux dernières nouvelles

- Finition et impression de la carte électronique pour le ROS
- Mise à jour de la CAO pour l'intégration des nouveaux capteurs
- Continuer la programmation des actionneurs et du lidar

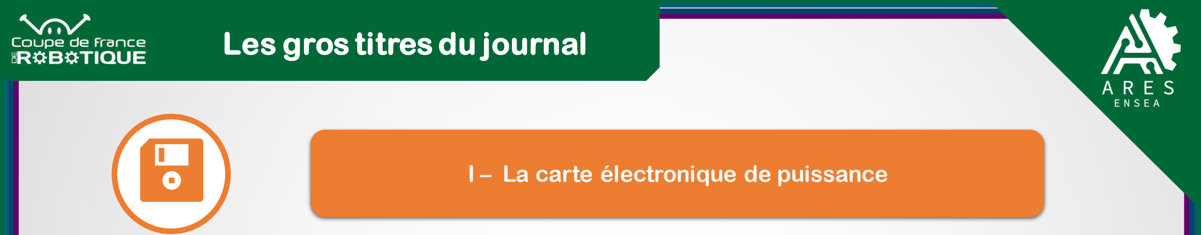
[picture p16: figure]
Les gros titres du journal; I – La carte électronique de puissance

3

II – Modification de l'envoi de données lidar

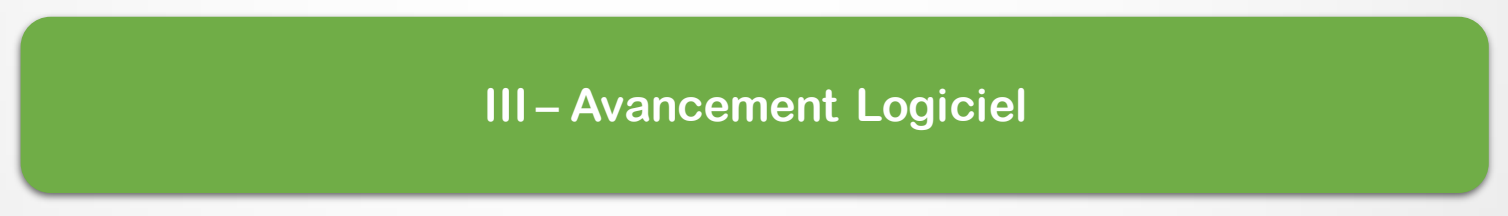
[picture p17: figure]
III – Avancement Logiciel
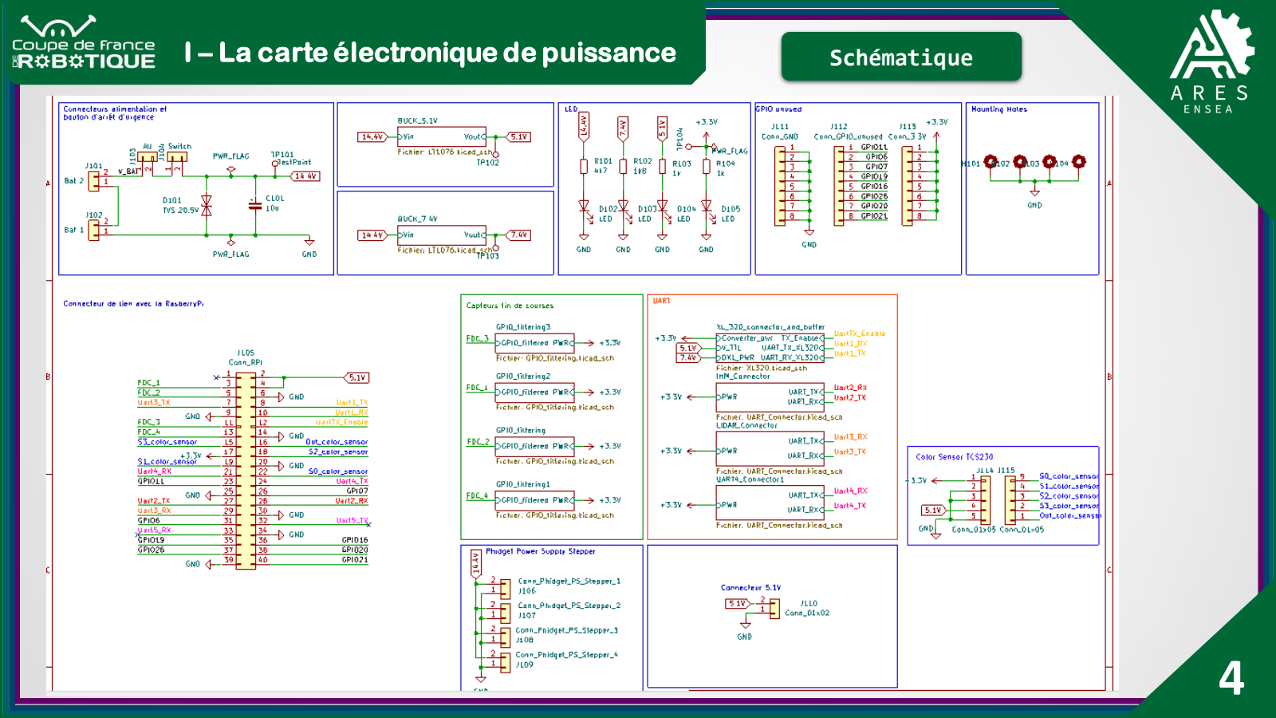
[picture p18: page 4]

4

I – La carte électronique de puissance | Schématique

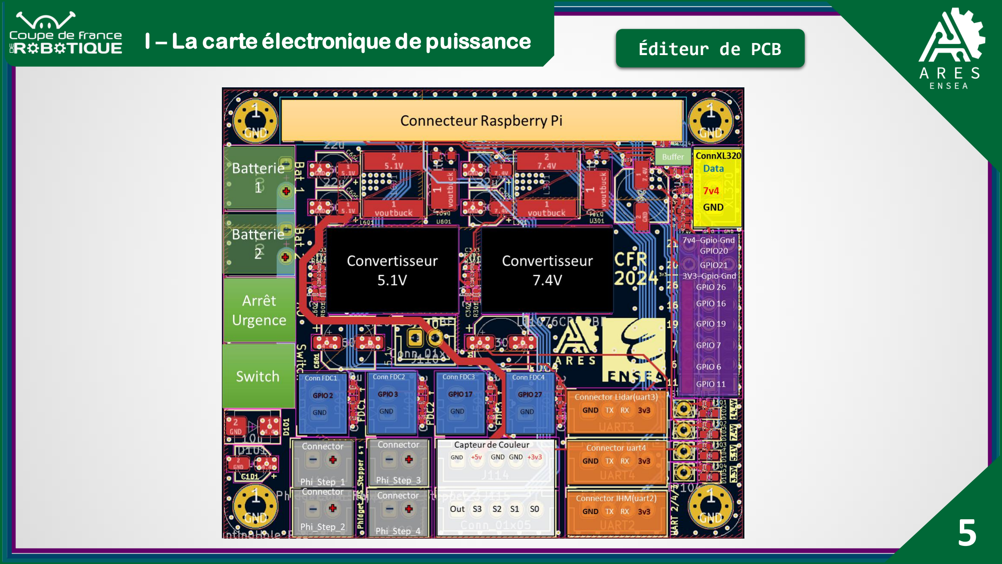
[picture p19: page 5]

5

I – La carte électronique de puissance | Éditeur de PCB

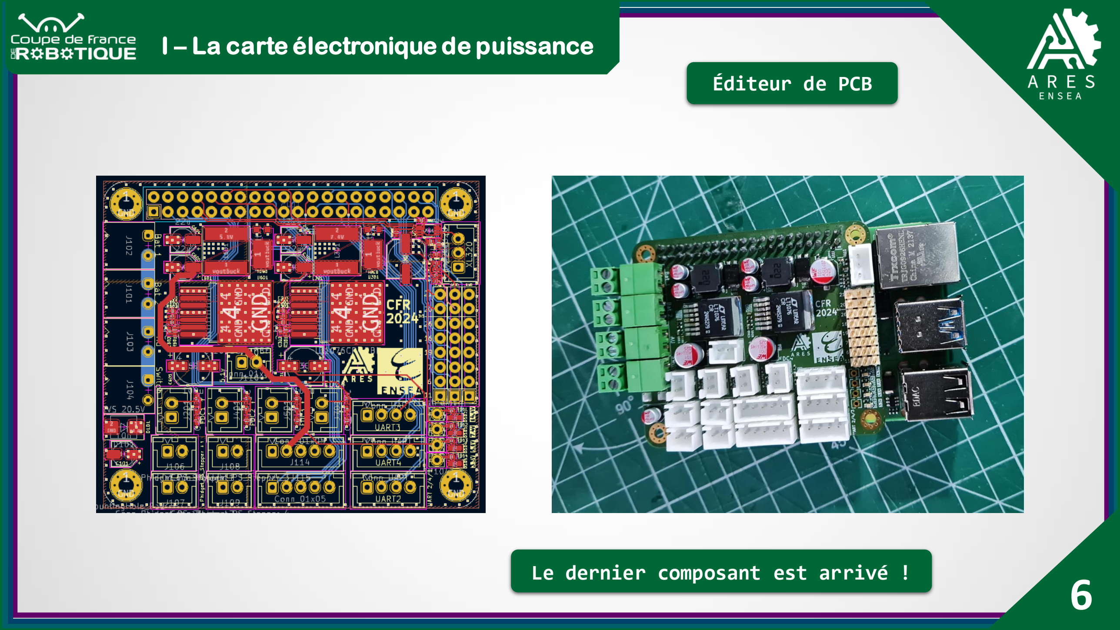
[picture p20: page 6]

6

I – La carte électronique de puissance Éditeur de PCB

Le dernier composant est arrivé !

### Mise à jour de la CAO

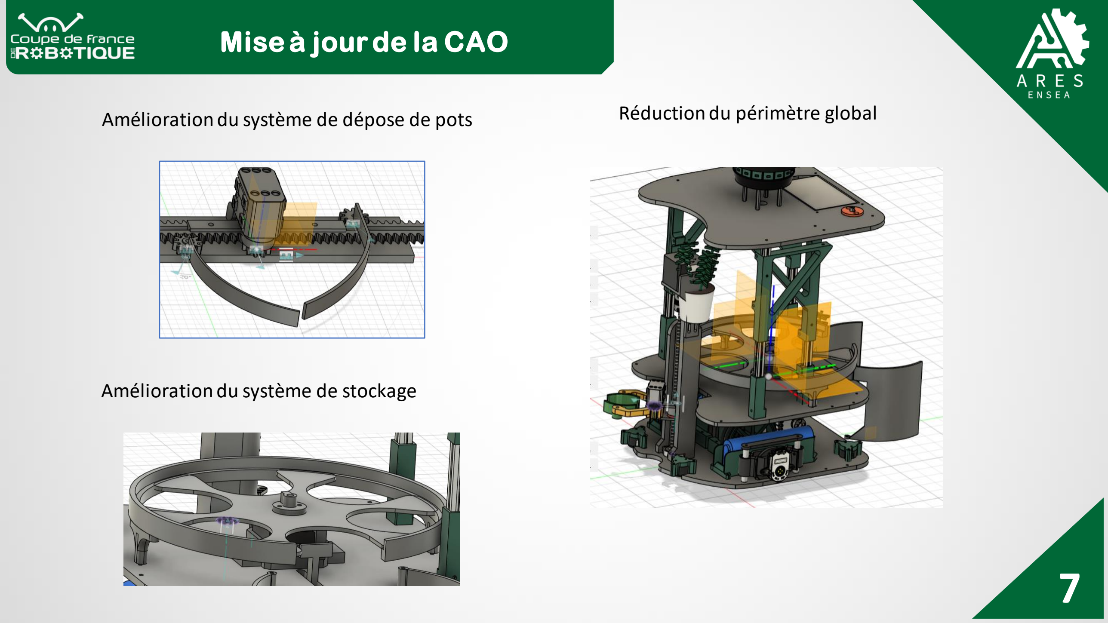
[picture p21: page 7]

7

Réduction du périmètre global Amélioration du système de dépose de pots

Amélioration du système de stockage

8

### II – Envoi de données du lidar

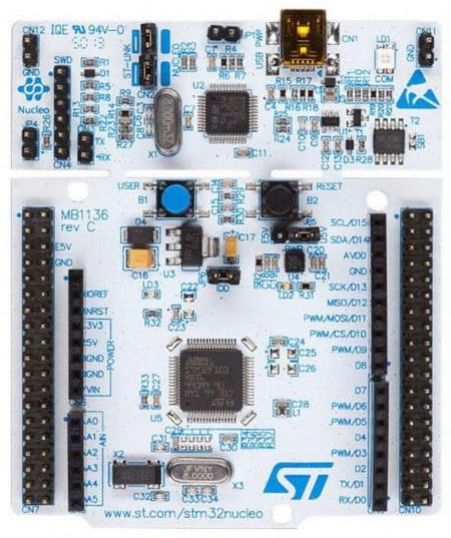
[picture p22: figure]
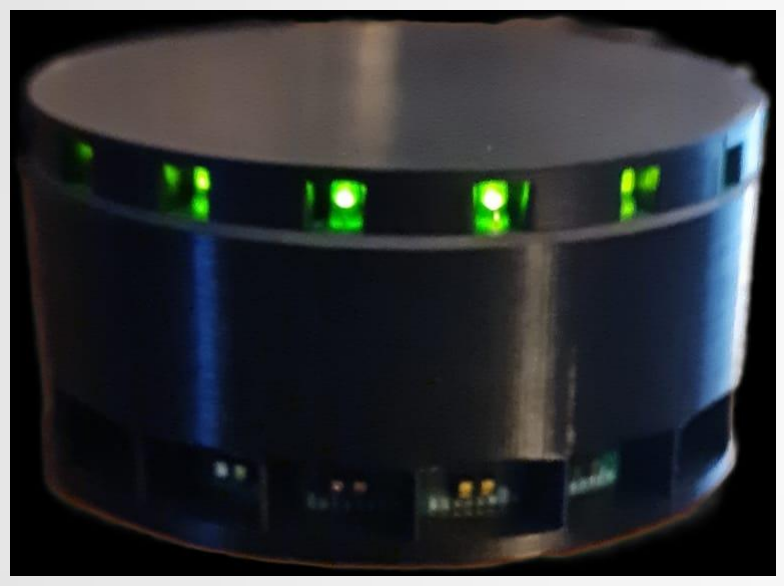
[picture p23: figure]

LidarDistance

Distance

9

### II – Envoi de données du lidar

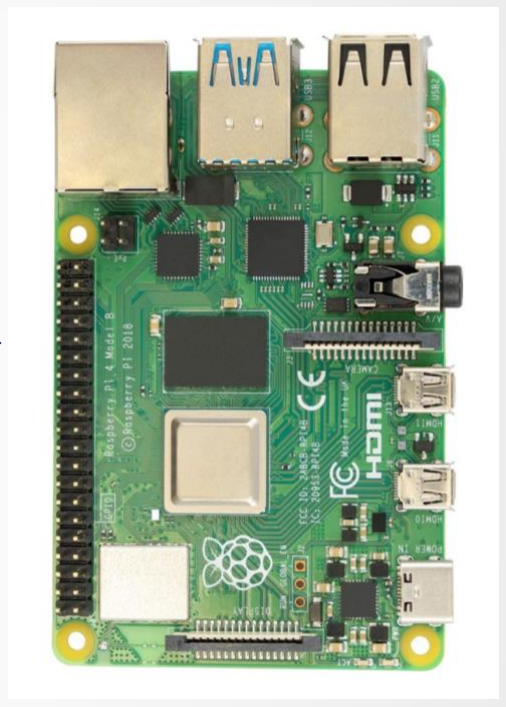
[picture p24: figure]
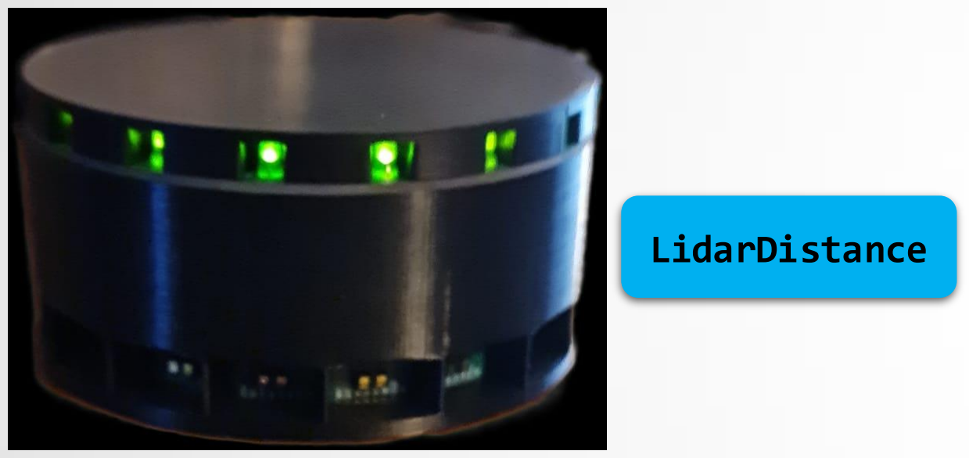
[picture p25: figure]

LidarDistance | Distance

### II – Deux écoles

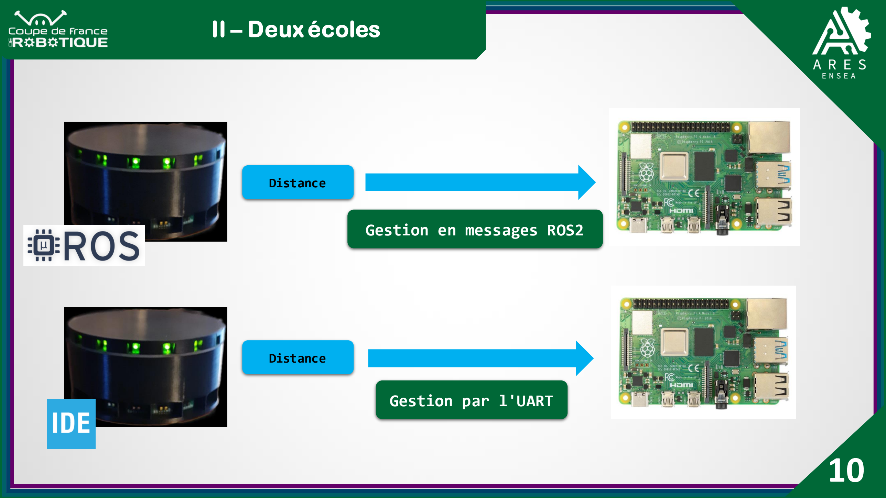
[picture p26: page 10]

10

Distance

Distance

Gestion par l'UART

Gestion en messages ROS2

11

### II – Mon planning

12

### II – Ça roule ?

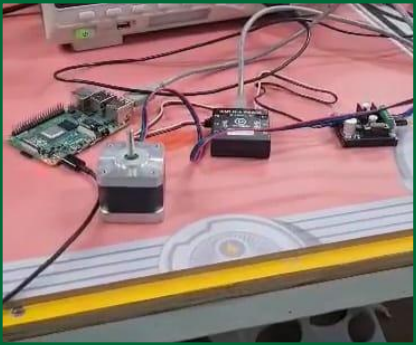
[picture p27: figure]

13

### III – Avancement logiciel

Stop_All

Les topics ROS2 | Speed_Factor
| Cmd_vel
| Odom

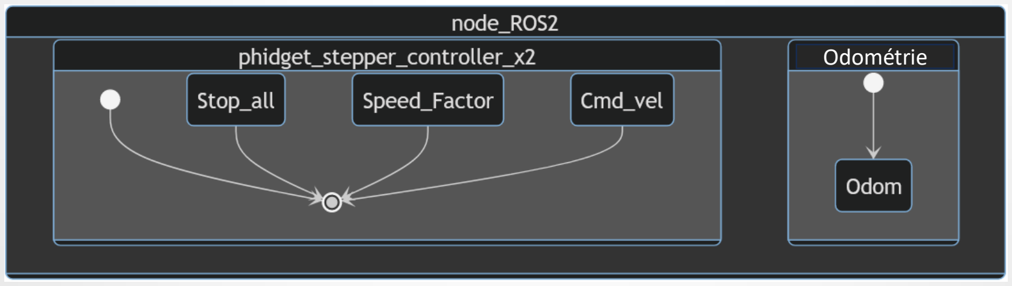
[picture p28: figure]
Odométrie

### III – Asservissement Phidgets

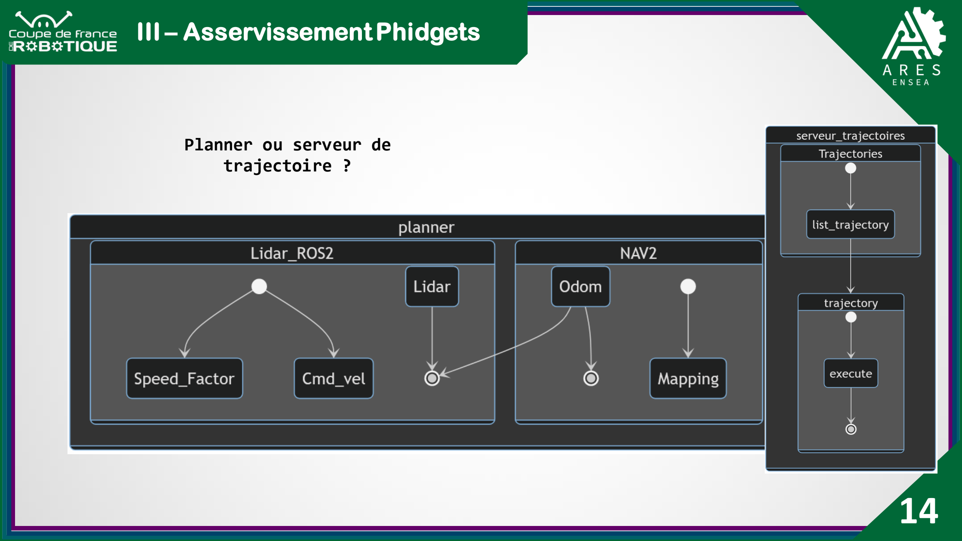
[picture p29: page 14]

14

Planner ou serveur de
trajectoire ?

15

### V – Dans le prochain épisode

- Soudage des autres cartes électroniques pour le ROS
- Impression de la dernière version des pièces du robot
- Continuer la communication lidar
- Faire une suite de mouvements avec le robot

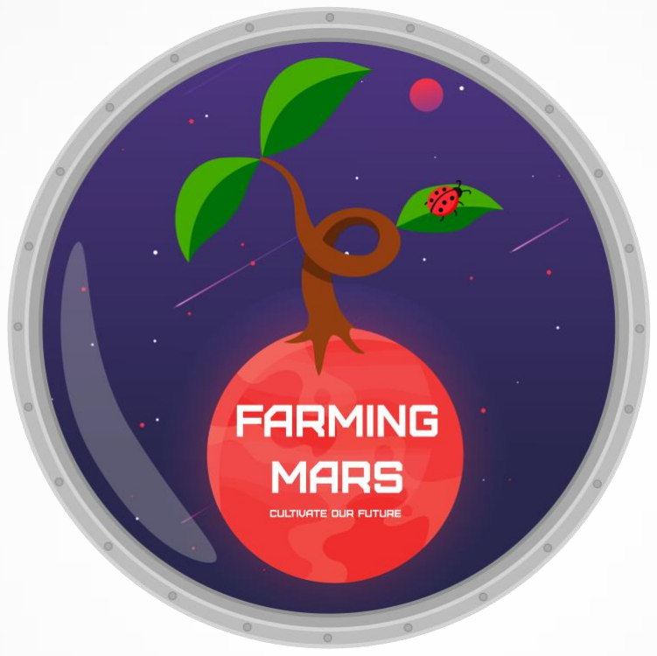
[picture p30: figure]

# Merci de votre écoute !

16

BICHEMIN Fannie
FAGET Nathan
THIONGANE Ousmane
WEIDLE Rémi

## Des questions ?

### 12 Mars 2024

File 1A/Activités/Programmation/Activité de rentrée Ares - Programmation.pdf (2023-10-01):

# Activité de rentrée

2023

# – Partie programmation –

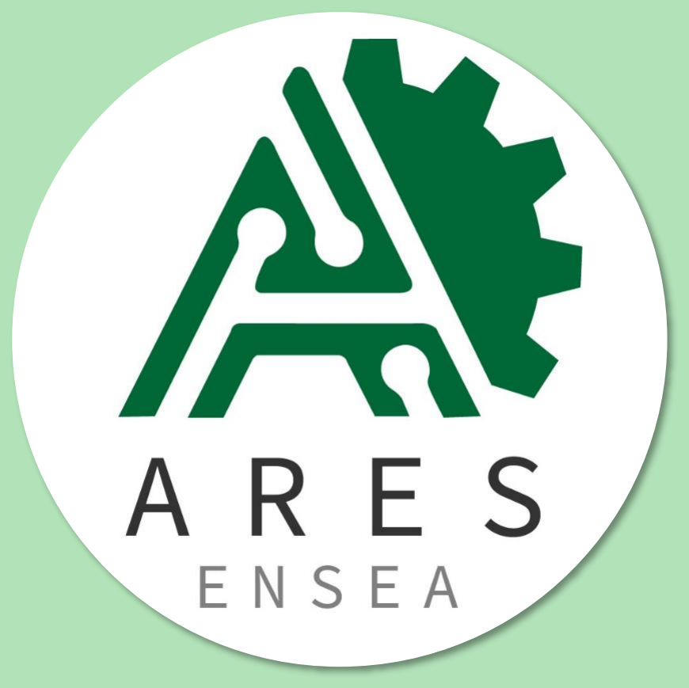
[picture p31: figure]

# Le mot du président

Bonjour à toi qui lit ce petit livret ! Cette activité de rentrée a pour but de te faire découvrir un peu les bases de la programmation sur microcontrôleur avec Mbed, afin de te familiariser un peu avec quelques concepts que tu pourrais rencontrer au cours de ta scolarité ou tes projets personnels. En fin de livret se trouve une introduction à STM32 Cube IDE, le logiciel que l’on utilise en cours à la place de ce qu’on va utiliser aujourd’hui, vous pourrez y jeter un œil après la séance si l’envie vous prend. Et ce n’est pas dramatique si vous ne comprenez pas tout ce qui y est expliqué, on n’est qu’au semestre 5 après tout, et vous n’allez le prendre en main qu’au semestre 6 ! L’ambition de ce livret est également de te faire découvrir petit à petit le local d’Ares et ce qu’on peut y faire en son sein, alors n’hésite

pas à en faire le tour pendant ou après l’activité.

# Amusez-vous bien !

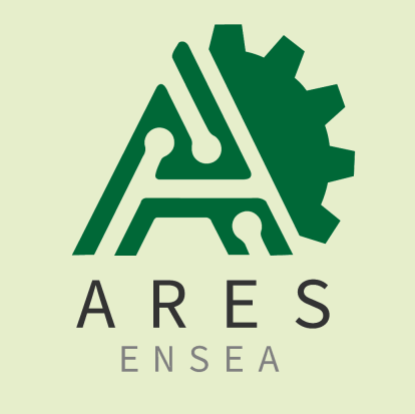
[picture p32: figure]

# Au sommaire

Programmation Mbed – Prérequis & Conseils | 4

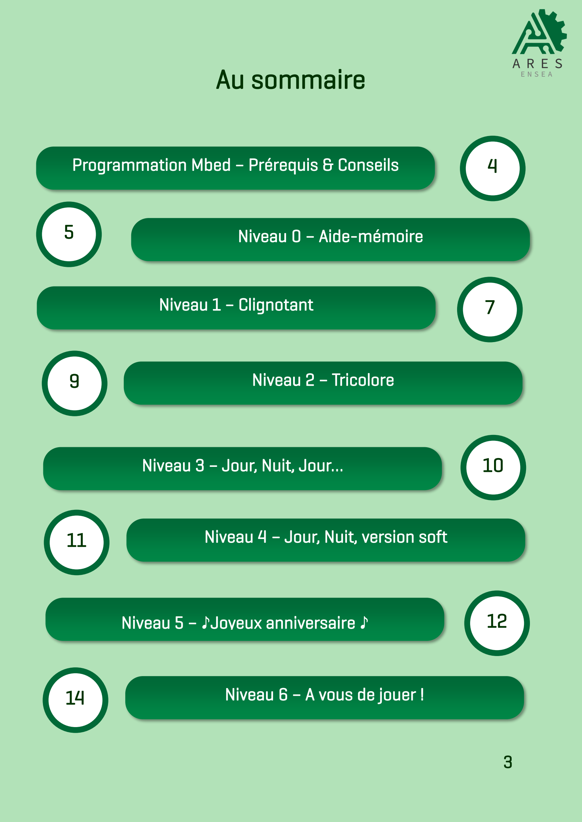
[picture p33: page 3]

5 | Niveau 0 – Aide-mémoire
Niveau 1 – Clignotant | 7
9 | Niveau 2 – Tricolore
Niveau 3 – Jour, Nuit, Jour… | 10
11 | Niveau 4 – Jour, Nuit, version soft
Niveau 5 – ♪Joyeux anniversaire ♪ | 12
14 | Niveau 6 – A vous de jouer !

# Programmation Mbed – Prérequis & Conseils

Tout d’abord, rendez-vous sur le logiciel en ligne Arm Keil Studio (studio.keil.arm.com). Connectez-vous avec les identifiants suivants : Adresse email : ares.X@outlook.fr (Remplacer le « X » par votre couleur de clan, par exemple « rouge », « noir », etc.)
Mot de passe : Aresensea95!

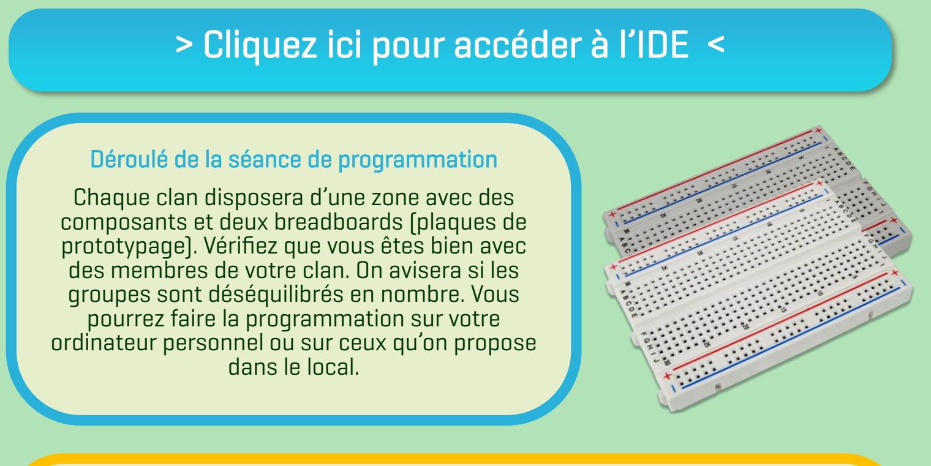
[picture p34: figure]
> Cliquez ici pour accéder à l’IDE <; Déroulé de la séance de programmation; dans le local.

Chaque clan disposera d’une zone avec des composants et deux breadboards (plaques de prototypage). Vérifiez que vous êtes bien avec des membres de votre clan. On avisera si les groupes sont déséquilibrés en nombre. Vous pourrez faire la programmation sur votre ordinateur personnel ou sur ceux qu’on propose

Conseils (qui vont seront utiles même plus tard !)
- Ne pas oublier les « ; » à la fin de chaque instruction
- Faire attention aux minuscules/MAJUSCULES dans les variables : rouge ≠ Rouge
- Vérifiez si le programme est bon avec la coloration syntaxique
- Regarder si la carte est bien détectée par le programme
- Ne pas frapper sa machine (ou son voisin) si ça ne fonctionne pas !

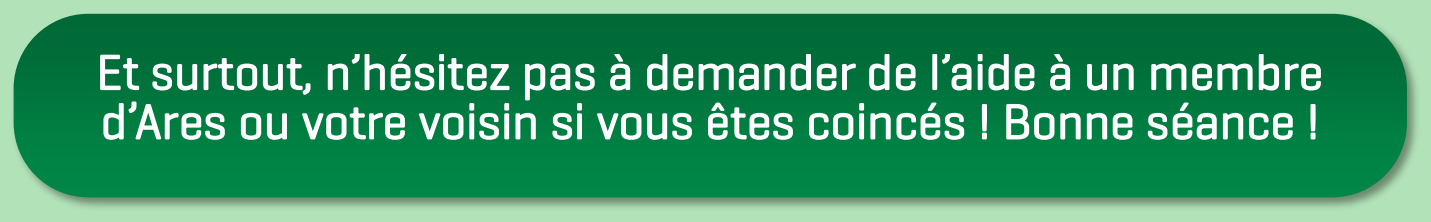
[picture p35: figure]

### Et surtout, n’hésitez pas à demander de l’aide à un membre d’Ares ou votre voisin si vous êtes coincés ! Bonne séance !

# Niveau 0 – Aide-mémoire Langage C++ et fonctions Mbed

Les variables | Les opérateurs
int : entier naturel codage sur 4 octets 31; 2 31 − 1] [−2 | float : nombre à virgule codage sur 4 octets | Arithmétiques : +, -, *, /, % Affectation : =, +=, -=, %=, |=, ^=, <<=, >>= Logique : &&, ||, <, >, <=, >=, ==, !=
char : caractère codage sur 1 octet [−128; 127] | double : nombre à virgule codage sur 8 octets
Condition | | Boucles
if (x < 3) { printf(“x est inférieur à 3”); } else { printf(“x est supérieur ou égal à 3”); } | int x = 0; while (x < 5) { printf(“coucou\n”); x++; } | int somme = 0; for (int i = 0; i < 100; i++) { somme += i; }
Directives de préprocesseur | Les tableaux
//Inclusion d’une bibliothèque, ici mbed #include “mbed.h” //Lors de la compilation, tous les N du code seront remplacés par des 7 #define N 7 | #define SIZE 5 #define SIZE2 3 //Exemples de tableaux à 1 dimension int tab[SIZE] = {1, 9, 0, 1}; char tabchar[SIZE2] = {“a”, “r”, “e”, “s”}; //Initialisation du premier tableau For (int = 0; i < SIZE; i++) { tab[i] = 0; }

Fonctions Mbed

DigitalOut myDigitalInput(pin); | Définir le type d’une broche numérique (DigitalIn = entrée, DigitalOut = sortie).
myDigitalInput = 1; | Définir l’état d’une broche numérique (HIGH = 1, LOW = 0)
int state = myDigitalInput.read(); | Lire l’état d’une broche.
ThisThread::sleep_for(1000ms); | Création d’une temporisation de 1000 ms = 1 seconde.
AnalogIn myAnalogInput(pin); | Définit le type d’entrée d’une broche analogique (A0, A1, …)
PwmOut myPwmOutput(pin); myPwmOutput.write(dutyCycle); | Crée un signal PWM de rapport cyclique dutyCycle ∈ [0,1] (Pour info, PWM ≡ Modulation de Largeur d’Impulsion)
void tone(int frequency) { myPwmOutput.period(1.0 / frequency); myPwmOutput.write(0.5); } | Fonction permettant de jouer une fréquence « frequency » avec un buzzer. Après l’avoir écrite, on peut l’appeler en écrivant par exemple pour jouer la note DO : tone(262);
myPwmOutput.write(0.0); | Éteint un signal PWM (Pratique pour éteindre un buzzer !).
InterruptIn signal(pin); | Création d’une interruption.
signal.rise(&fonction); | Exécute la fonction « fonction » à la montée du signal (remplacer rise par fall pour la descente du signal).

# Niveau 0 – Aide-mémoire : Pinout Configuration

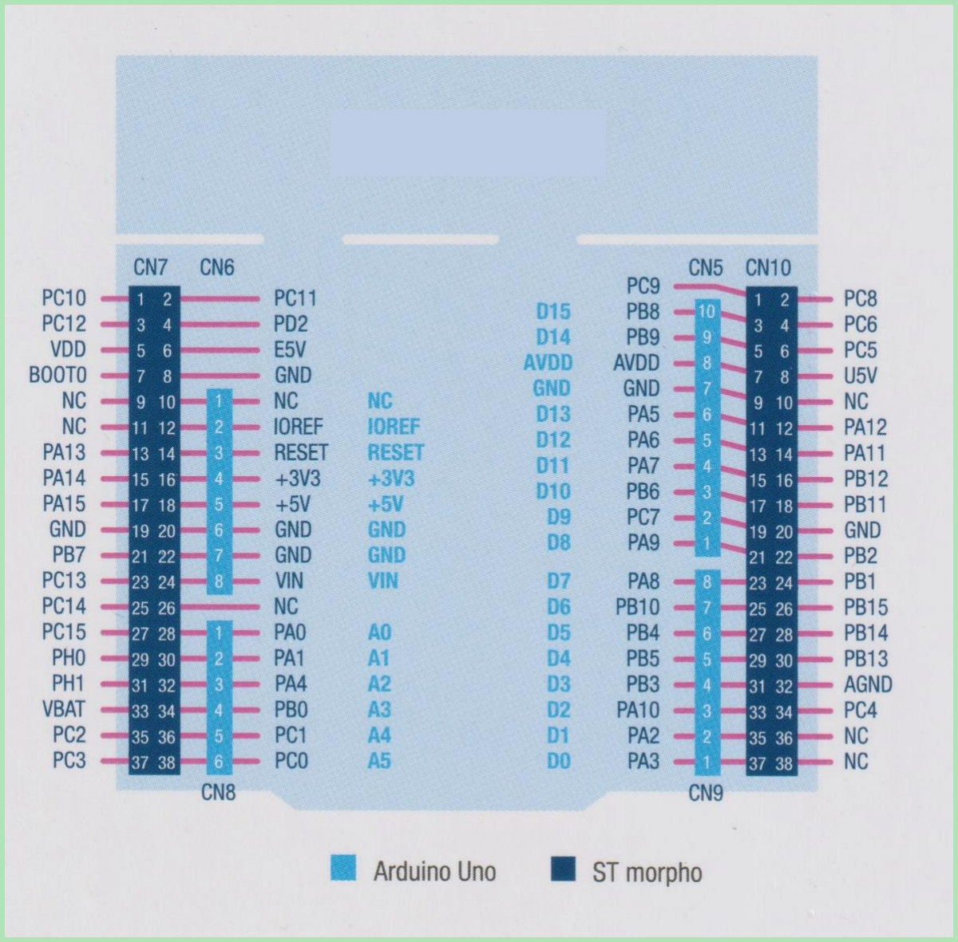
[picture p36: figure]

# Niveau 1 – Clignotant

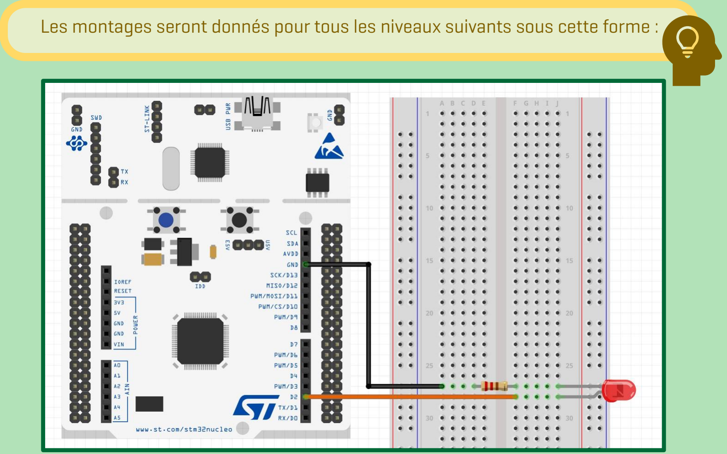
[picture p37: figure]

Et comme à Ares nous sommes généreux, voilà en page suivante un code qui vous permettra d’allumer la LED et son explication :

Les montages seront donnés pour tous les niveaux suivants sous cette forme :


### Mission : Faire clignoter la LED en changeant son état toutes les secondes

La broche à laquelle est
connectée la LED est « D2 ». Dans le pinout configuration de l’aide-mémoire, on voit que cela correspond à PA10.

La LED étant une sortie numérique, on définit la broche ledPin en tant que telle en précisant son type « DigitalOut ».

Après téléversement du
code sur votre carte,
tout le code compris en
dehors de la boucle
while (1) { } sera lancé
une fois.

Après téléversement du
code sur votre carte, tout le code compris dans le
while (1) { } s’exécutera à l’infini !
Dans la boucle infinie, on écrit ledPin = 1 pour la mettre à l’état haut et ainsi l’allumer !

Le saviez-vous ? : Le langage de programmation utilisé pour coder sur Mbed est le C++. Il est souvent utilisé pour coder des applications mobiles, des jeux vidéo, des logiciels de bureautique, en robotique…

# Niveau 2 – Tricolore


### Mission : Changer de manière successive l’état des 3 LEDs

# Niveau 3 – Jour, Nuit, Jour…


### Mission : Commander l’allumage de la LED grâce à un bouton

Peut-être que pout connaître l’état du bouton, une fonction existe pour lire l’état d’une broche numérique… Peut-être même qu’elle est dans l’aide-mémoire. La vie est bien faite non ?

# Niveau 4 – Jour, Nuit, version soft


### Mission : Faire varier l’intensité de la LED émise à l’aide d’un potentiomètre

La broche du potentiomètre est connectée à un port analogique. Hmm… Analogique, analogique, analog… Et la LED est branchée à une broche PWM… Hmm…

# Niveau 5 – ♪ Joyeux anniversaire ♪


Fréquences des notes et partition simplifiée de « Joyeux anniversaire » :

Notes | Do | Do# | Ré | Ré# | Mi | Fa | Fa# | Sol | Sol# | La | La# | Si | Do2

Sol
appuyé

### Mission : Jouer « Joyeux anniversaire » lorsque le bouton est


### Mission bonus : Points supplémentaires pour votre clan si vous arrivez à jouer une autre mélodie !

Il y’a 25 notes dans jouées « Joyeux anniversaire ». On peut utiliser la méthode bourrine qui serait d’écrire 25 fois tone() pour chaque note, mais je suis sûr qu’il y’a une solution plus rapide ! Une couleur de note correspond à une durée différente, pensez à varier les délais entre celles-ci. Et par pitié, n’oubliez pas d’éteindre le buzzer après un certain temps dans votre code avec .write(0.0) !

# Niveau 6 – À vous de jouer !


FIN.

### Mission : Avec le matériel proposé et les autres membres de votre clan, réalisez quelque chose d’original !

N’oubliez pas de brancher des résistances aux composants qui en ont besoin. Ils vous remercieront en ne produisant pas de fumée !

# Micro-introduction à STM32


# Deux différences majeures avec Mbed

Ici à l’ENSEA, l’école nous apprend à utiliser STM32 Cube IDE, un logiciel un peu plus complexe, mais très important car il est utilisé au sein de beaucoup d’entreprises.

### On peut programmer en langage C++, mais aussi en langage C. C’est ce dernier qui est

enseigné à l’école.

### Pour définir les entrées/sorties du microcontrôleur, on peut le coder à la main mais aussi le générer automatiquement grâce

à l’interface proposée par STM32.

# Niveau 1 EX – Clignotant version STM32


Le montage est le même, que celui du niveau 1, mais pour faire comme si c’était nouveau, j’ai mis une LED bleue.

Mission EX : Faire clignoter la LED en utilisant STM32.


Pour vous expliquer brièvement ces deux images : Après avoir installé STM32, je crée un nouveau « projet STM32 » en sélectionnant la bonne carte et le bon langage cible (Langage C).


Une fois le projet créé (et c’est bien long la première fois…) je vais pouvoir définir mes broches avec le fichier « .ioc » qui nous donne une vue graphique du microcontrôleur.

(GPIO_Output).

Je n’oublie pas de générer le code associé en appuyant sur ce bouton , sinon la configuration ne sera pas prise en compte dans le code !

Comme vous avez bonne mémoire, vous savez que la broche « D2 » est celle qui correspond à « PA10 » sur le microcontrôleur, on la configure donc directement en sortie


Et voilà une belle LED qui clignote ! (Ce n’est qu’une image donc ça ne clignote pas, mais je vous promets que ça fonctionnait quand je l’ai fait !)

J’écris ensuite mon code dans le fichier « main.c » :

J’utilise une des fonctions de la librairie HAL, déjà intégrée à STM32. HAL_GPIO_TogglePin() permet de changer l’état de la broche définie en paramètre, ici PA10.

On retrouve notre amie la boucle while (1) {} ! On peut aussi écrire while (true) { }.

HAL_Delay nous permet de faire l’attente de 1000ms soit 1 seconde.

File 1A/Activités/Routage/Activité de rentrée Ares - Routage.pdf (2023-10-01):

# Activité de rentrée

2023

# – Partie routage –


# Au sommaire

Routage – Prérequis & Conseils; Niveau 0 – Introduction; Niveau 1 – Schématique; Schématique – Placement des composants; Schématique – Numérotation des composants; Schématique – Analyse de la qualité du schéma; Schématique – Assignation des empreintes; Niveau 2 – Routage; Routage – Importation des composants; Routage – Contours du PCB; Routage – Plan de masse; Routage – Placement des composants; Routage – Classes d’équipotentielles; Routage – Routage !; Routage – Analyse de la qualité du routage

# Routage– Prérequis & Conseils

Tout d’abord, téléchargez KiCad sur votre machine si ce n’est pas déjà fait.

> Cliquez ici pour télécharger KiCad <

Déroulé de la séance de routage
Pour cette séance, pas besoin de vous regrouper par clan. Vous pourrez faire le routage sur votre ordinateur personnel ou sur ceux qu’on propose dans le local. S’il n’y a pas assez d’ordinateurs, mettez-vous à plusieurs par poste en essayant de vous partager le travail.

Conseils
- – Ce livret est beaucoup plus long que celui de programmation donc n’hésitez pas à le continuer chez vous, surtout que la fin est fun !
- La plupart des missions possèdent une icône représentative du bouton sur lequel il faut appuyer dans KiCad.
- Touches « A », « B », « V », etc. Beaucoup de raccourcis sont utiles !
- Il faut éviter au maximum les angles droits lors de la création des pistes !
- Ne pas frapper son voisin ou qui que ce soit en fait.

séance !

### Et une fois de plus, n’hésitez pas à demander de l’aide à un membre d’Ares ou votre voisin si vous êtes coincés ! Bonne

# Niveau 0 – Introduction

Nous allons essayer de réaliser un petit circuit imprimé avec des composants simples (LED, buzzers, résistances…) qui pourrait par la suite être branché à une carte électronique :


Cette réalisation se fait en deux étapes :
- Schématique : C’est là où on réalise le schéma du montage, un peu comme les schémas qu’on trouve en cours d’électronique.
– Routage : C’est là qu’on choisit la position des différents composants, que l’on connecte entre eux en les routant.

# Niveau 1 – Schématique

### Mission : Créer un projet KiCad et ouvrir l’éditeur de


### schématique

Vous pouvez modifier le cartouche en bas à droite de votre schématique en double-cliquant dessus. On y ajoute en général la date, la version, le titre, son nom en commentaire…

Le saviez-vous ? : Les labels locaux & globaux permettent de relier des composants sans avoir à le relier par un fil. C’est très pratique pour améliorer la lisibilité d’un schéma avec beaucoup


Un schéma sans label à gauche, un autre avec label à droite. Les deux schémas

Label local : Label fonctionnel pour une seule page du projet

Label global : Label fonctionnel pour toutes les pages d’un même projet

# Schématique – Placement des composants


Nous allons besoin de placer les composants nécessaires pour notre carte. En voici la liste : – 3 LEDs (LED)
– Un connecteur mâle à 7 broches (Conn_01x07_Pin) – 4 résistances (R)
– 1 bouton poussoir (SW_Push) – 1 buzzer (Buzzer)

### Mission : Ajouter tous les composants nécessaires au schématique

Le raccourci-touche « A » permet aussi d’ajouter des composants !


Le saviez-vous ? : Pour éviter les erreurs lors de la vérification du schéma, il faut placer un PWR_FLAG en parallèle au +5V et à la masse. Il permet de dire à KiCad d’où viendra l’alimentation.

### Mission : Relier les composants entre eux avec des fils et des

labels et mettre l’alimentation (+5V) et la masse (GND).

# Schématique – Numérotation des composants

### Mission : Passer par l’outil de numérotation des composants vérifier la numérotation

# Schématique – Analyse de la qualité du schéma


### Mission : Exécuter l’ERC (Electrical Rules Checker) et corriger son schéma jusqu’à ce qu’il n’y ait plus d’erreurs

GG à toi si tu n’avais aucune erreur dès le début !

# Schématique – Assignation des empreintes


Le schéma est réalisé, mais il faut maintenant donner à chacun des composants une empreinte qui va représenter sa forme et ses dimensions sur la carte électronique. On utilise pour ça l’outil d’affectation d’empreintes.

Le saviez-vous ? : L’outil est divisé en trois colonnes :
1 – Les librairies d’empreinte disponibles
2 – Les symboles de votre schéma et leur empreinte associée (pas d’empreintes pour le moment)
3 – Les empreintes pour chacun des composants

Le saviez-vous ? : Pour vous donner un coup de main il existe trois filtres :
1 – Filtre des empreintes définies pour le symbole sélectionné 2 – Filtre par nombre de broches du symbole sélectionné
3 – Filtre par librairie sélectionné dans la colonne de gauche

### Mission : Affecter les empreintes suivantes à chacun des composants :

Une fois tout cela de fait et plus aucune erreur sur l’ERC, Nous allons pouvoir passer au design du PCB.

# Niveau 2 – Routage

### Mission : Ouvrir l’éditeur de PCB KiCad


C’est ici que l’on va concevoir le circuit imprimé !

# Routage – Importation des composants


### Mission : Importer les composants depuis votre schéma vers

l’éditeur de PCB et les déposer.

# Routage – Contours du PCB

### Mission : Sélectionner le Layer « Edge.Cuts » et tracer le


### contour de votre PCB avec les outils « Ligne » et « Arc de cercle »

Prévoyez environ 30mm pour pouvoir placer tous les composants à l’intérieur. Après si vous faites moins, on ne vous en voudra pas vu qu’il sera plus écologique et moins cher !

# Routage – Plan de masse

### Mission : Sélectionner le Layer « F.Cu » et cliquer sur « Add a


### filled zone ». Sélectionner « GND » puis valider, et encadrer le contour du PCB avec. Faire pareil avec le Layer « B.Cu »

Le saviez-vous ? : La masse est le signal le plus important du PCB, puisqu’elle se trouve quasiment partout. Faire un plan de masse sur les deux faces du PCB permet entre autres de :
– Réduire l’impédance des fils au minimum – Connecter automatiquement à la masse les composants qui en ont besoin
– C’est plus écologique !

Une fois ça de fait, il faudra fréquemment réactualiser le plan de masse en appuyant sur la touche « B »

# Routage – Placement des composants

### Mission : Placer les composants comme bon vous semble


sur le schéma, puis regénérer le plan de masse (B).

Vous pouvez avoir un aperçu 3D de votre carte en allant sur le menu « Affichage » puis « Visu 3D » Qu’elle est belle !


# Routage – Classe d’équipotentielles

Vous pouvez ajuster l’écart entre les points de la grille en faisant un clic droit dans la zone de travail, puis en sélectionnant « Grille ». Vous pourrez ainsi placer les composants de manière plus précise.

# Routage – Classes d’équipotentielles

### Mission : Aller dans la section « Net Classes » du « Board

Setup ».

### Mission : Modifier les paramètres suivants de la classe Default: Clearance : 0.3mm Track width : 0.3mm Via Size : 0.8mm Via Hole : 0.4mm

Ainsi tous les signaux avec la catégorie Default auront des pistes avec ces paramètres. Pratique !

### Mission : Avec le premier bouton « + », créer une deuxième classe « Power » et lui attribuer les


### paramètres : Clearance : 0.3mm Track width : 0.5mm Via Size : 1.2mm Via Hole : 0.6mm

### Mission : Avec le deuxième bouton « + », Créer tous les signaux du circuit (+5V, GND, LED1,…) et leur

attribuer la bonne classe (Power pour +5V et GND, Default pour les autres).

Est-ce qu’on ne passerait pas au routage maintenant ?

# Routage – Routage !

### Mission : Relier toutes les pistes comme indiquées par le


chevelu.

Bon courage ! Si vous avez des difficultés à tous relier, il faudra peut-être revoir la position de certains composants, mais vous pouvez aussi router sur la face arrière « B.Cu ».


Une autre idée serait d’alterner entre les deux couches en passant par un « trou ». C’est le rôle d’une via. Lorsque vous tracez une piste, appuyez sur « V » et une via apparaîtra.

une fois que tout est fini !

Vous pouvez écrire du texte sur une des faces de votre PCB et regénérer votre plan de masse pour avoir votre texte en relief. Et en parlant de plan de masse, n’oubliez pas de le regénérer

# Routage – Analyse de la qualité du routage


### Mission : Exécuter le DRC (Design Rules Checker) et vérifier

corriger les erreurs éventuelles.


## Et voilà un super PCB !

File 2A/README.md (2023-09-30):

# 2A
Ce dossier regroupe les fichiers réalisés par les étudiants en deuxième année de l'association

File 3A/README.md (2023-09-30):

# 3A
Ce dossier regroupe les fichiers réalisés par les étudiants en troisième année de l'association

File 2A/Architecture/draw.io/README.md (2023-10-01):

# draw.io
Dossier contenant les fichiers ".drawio" du projet.

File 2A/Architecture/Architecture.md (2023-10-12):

# Architecture de l'asservissement :

```mermaid
flowchart TD;
  DebutT[/"`Ramassage des objets`"\] -->Detect[/"`Detection d'un objet`"/]-->Objet{Objet ?};
  Objet-->|non| Detect[/"`Detection d'un objet`"/];
  Objet-->|oui| Plante{Plante ?};

  Plante -->|oui| ObjetPlante["objet = plante"]-->rigide[/"`Detection du type de plante`"/];
  Plante -->|non| ObjetPot["objet = pot"];

  rigide-->Rigide{rigide ?};
  Rigide-->|non|TypeFragile["Type = Fragile"];
  Rigide-->|oui|typerigide["Type = Rigide"];

  TypeFragile-->Potpresent{Pot présent dans\n un emplacement \nde stockage ?};
  Potpresent--->|oui|AX12pot;
  Potpresent--->|non|Partir;

  typerigide-->Vide2{"Eplacement vide\n pour plante rigide ?"};
  Vide2-->|non| EmplacementPot{"Emplacement\n avec un pot ?"};
  Vide2-->|oui| AX12vide["rotation de l'AX12 de l'espace \n de stockage vers l'emplacement libre"] ;
  EmplacementPot-->|oui| AX12pot["Rotarotation de l'AX12 vers l'emplacement \n du stockage contentant un pot "];
  EmplacementPot-->|non| Partir;
  ObjetPot-->ObjetPot?{Eplacement vide\n disponible ?};
  ObjetPot?-->|non| Partir(["`ordre de partir`"]);
  ObjetPot?---->|oui| AX12vide;
  AX12vide-->VerouillagePince;
  AX12pot-->
  VerouillagePince("`Verouillage de la pince`")==>
  MontéPince("`Montée de la pince avec l'objet\n grâce à l'ascenseur `")==>
  Arrivee{"Arrivée au niveau \n de l'espace \nde stockage ?"};
  Arrivee-->|non| MontéPince;
  Arrivee-->|oui| Ouverture["ouverture de la pince pour l'acher l'objet"]-->
  Fin(["`Fin stockage`"]);
```

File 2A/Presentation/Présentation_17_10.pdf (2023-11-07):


# Présentation de projet

## Coupe de France de Robotique

## - Architecture du projet -

1

BICHEMIN Fannie
FAGET Nathan
THIONGANE Ousmane
WEIDLE Rémi

## Présentation de projet

### 17 octobre 2023

## Sommaire

II – Architecture ROS2

I – Logigramme d'asservissement & Diagramme d'architecture

III – Architecture logicielle

### I – Logigramme d'asservissement


3

Cas 1

Cas 4

Cas 2

Cas 3

Visualisation du robot

### I – Logigramme d'asservissement


4


5

### I – Logigramme d'asservissement

6

### I – Logigramme d'asservissement



7

### I – Diagramme d'architecture

8

### II – Architecture ROS2

### III – Architecture logicielle


9

Machine à états du robot

### III – Architecture logicielle


10

Strat_MOVE

Strat_RWD

MPDS_GRID | MPDS_MOVE
| MPDS_RWD
| Ckpnt_SW

Match_END : prioritaire après 75-80s de match

### III – Réalisation de l'interface


11

Module PyQt5 de Python pour la GUI

But : Récupérer les coordonnées du robot via le code de l'année dernière "odometry.c"

Utilisation de la zone de calcul déportée ?

12

IV – À faire avant le prochain point

- Continuer à analyser ce qui a été réalisé les années passées (code du simulateur, du robot etc.)
- Terminer l'IHM de la Méthode des Points de Sûreté + tester la communication bluetooth entre un périphérique et l'IHM
- Demander à M.Fiack de contacter ses amis de chez INSTAR Robotics (et ça tombe bien parce que M.Fiack il est là en train de regarder notre présentation !)


# Merci de votre écoute !

13

BICHEMIN Fannie
FAGET Nathan
THIONGANE Ousmane
WEIDLE Rémi

## Des questions ?

### 17 octobre 2023

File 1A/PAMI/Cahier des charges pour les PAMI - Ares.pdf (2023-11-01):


# Un PAMI ? C’est quoi ça se mange ?

Un PAMI est un Petit Actionneur Mobile Indépendant, c’est un petit robot conçu par l’équipe afin réaliser des actions qui lui sont spécifiques. Par exemple cette année, les PAMI sont des coccinelles doivent polliniser des plantes en entrant en contact avec ces dernières, en terminant dans une des zones de son équipe, le tout en 10 secondes ! C’est donc ce genre de robot que vous allez construire, et comme vous n’en avez peut-être jamais fait, ce livret est là pour vous guider dans l’organisation de votre équipe et la conception de votre PAMI. Sachez également que la réalisation de votre PAMI est une des missions cruciales pour l’obtention de points pour Ares. Pour s’en convaincre, un petit calcul s’impose : Imaginons que le robot principal arrive à tourner de manière valide 5 panneaux solaires, mettre 3 plantes au bon endroit et retourner dans sa zone de recharge : Il fera 65 points. Prenons maintenant le même scénario mais cette fois, 3 coccinelles démarrent et rentrent chacune dans une zone de l’équipe : On passe à 80 points. Et 95 si chacune des trois entre en contact avec une plante ! Vous l’aurez vite compris, les PAMI représentent environ un tiers des points d’Ares s’ils sont bien réalisés (c’est beaucoup de points, pas vrai ?)

# L’Objectif de nos amis les PAMIs

Durant la phase de préparation, les coccinelles seront déposées dans la zone de départ des PAMI et doivent être contenues dans les limites de la zone. Les lignes colorées sur le vinyle et le bord de la table (sur ces 22mm d’épaisseur) font partie de la zone de départ.

Une équipe peut posséder autant de coccinelles qu’elle le souhaite, elles devront toutes être contenues dans la zone de départ des PAMI (15cm x 45cm) et ne sont pas empilables. Elles ont le droit de sortir de leur zone seulement après la 90ème seconde de match (invalidation de la coccinelle dans le cas contraire), les coccinelles auront jusqu’à la 100ème seconde pour atteindre leurs objectifs.

La coccinelle est validée comme étant en zone si tout ou une partie de sa projection verticale est dans une zone de dépose au sol ou dans une jardinière en fin de match.

La coccinelle n’a pas le droit de sortir une plante d’une zone, ou de faire entrer une plante dans une zone (invalidation de l’action de la coccinelle le cas échéant, et remise en place de la plante concernée).

Ce que dit le règlement

Zone de départ des PAMI (pour l’équipe jaune par exemple; pour l’équipe jaune)

Zones atteignables par les PAMI (toujours

une plante valide.

### 5 points par zone de dépose de l’équipe occupée

par au moins une coccinelle à la fin du match.

### Mission : Le PAMI doit entrer dans une zone de l’équipe et toucher une plante + toucher une plante ou un pot contenant

match

### 5 points supplémentaires par zone de dépose dans laquelle au moins une coccinelle est en contact avec une plante ou un pot contenant une plante en fin de


### ATTENTION : Si une coccinelle réalise ses actions dans une zone adverse, alors les points réalisés iront à l’autre équipe !


Puisqu’il y’a 6 zones (parterres + jardinières) nous pourrions aller jusqu’à 30 points en mettant un PAMI dans chaque zone et 60 s’ils touchent tous une plante. Mais pour commencer il vaut mieux se concentrer sur les zones simples (parterres) et se limiter à quelques PAMI (par exemple 3), sinon ça risque d’être difficile de tous les maîtriser.

# Les cases à cocher (Dimensionnement)

Un PAMI doit être plus grand qu’un cube de 60mm de côté.


La masse d’un PAMI ne doit pas excéder 1,5kg.

Un PAMI peut se déployer dans la limite d’une augmentation de 10cm de son périmètre.

Un PAMI peut se déployer et évoluer dans la limite d’une altitude de 35cm.

Un PAMI doit avoir une zone de 3x3cm pour accueillir l’autocollant avec le numéro de stand.

facile pour les arbitres).

Au niveau du design et des couleurs, n’hésitez pas à vous entretenir avec les autres groupes pour avoir des de PAMI qui soient harmonisés (ça sera plus

Si votre PAMI est fonctionnel, n’hésitez pas non plus à faire preuve d’imagination pour le rendre attractif pour le public/les médias, par exemple s’il arrive à bon port, il pourrait jouer une mélodie et devenir arc-en-ciel !

Les cases à cocher (Détection, BAU,

# Alimentation…)

robot lui-même.; tirette. Une fois enlevé, l’interrupteur change d’état et le robot démarre !

Les PAMI peuvent être démarrés en début de match par un cordon de démarrage (d’au moins 50 cm de long) ou bien durant le match par le

Les PAMI sont tenus de disposer d’un système de détection des robots adverse. Le système est destiné à empêcher les collisions entre les robots pendant un match. Ce point sera systématiquement vérifié lors de l’homologation.

Tous les PAMI doivent être équipés d’un bouton d’arrêt d’urgence rouge d’au moins 20mm de diamètre. Il sera placé au sommet du PAMI, dans une zone non dangereuse et immédiatement accessible par les arbitres à tout moment. Le bouton peut dépasser la hauteur réglementaire du système de 2,5cm.

Le saviez-vous ? Sur le robot principal, un interrupteur est appuyé avec le bout de la

Sympa le bonus de taille !


Pour ça plusieurs méthodes peuvent faire l’affaire : capteur ultrason, capteur TOF, mini lidar… à vous de voir lequel vous pensez maîtriser le mieux. Au passage je mets en lumière une contrainte qui pourrait vous poser des soucis : Le PAMI doit toucher une plante ou un pot en zone mais il ne doit rien percuter d’autre. Comment différencier une plante d’un autre obstacle ?

# Quelques pistes pour concevoir votre PAMI

Les sumobots ou les « presque-PAMIs »
Est-ce que vous saviez que les sumobots; zone en 10 secondes ?

rentraient pile-poil dans la zone de départ des PAMI ? et qu’ils peuvent aller dans une

Les sumobots peuvent servir de base à la conception de votre PAMI si vous ne savez pas exactement comment vous pourriez le réaliser. Ils fonctionnent avec un joystick et de la communication Bluetooth. Essayez de faire quelques tests sur la table avec : Aller dans une zone en 10 secondes, toucher une plante (avec ou sans pot), etc.

similaire.

Nous n’avons pas de balance à Ares malheureusement (peut-être chez Epicuria ?), mais il serait intéressant de peser le sumobot, afin de voir si votre PAMI devra être plus léger ou si vous aurez de la marge avec une structure

Les sumobots pourraient être des PAMI mais ils leur manquent des éléments cruciaux, donc ils ne peuvent pas concourir en l’état : Tirette de démarrage, Bouton d’arrêt d’urgence, système de détection. À vous de repenser leur design pour en faire de véritables PAMI.


> Lien du dossier GitHub pour les sumobots < (https://github.com/AresEnsea/Ares/tree/main/Robot%20sumo)

sumobot (code, PCB, …)

### Mission : Récupérer les dossiers liés au projet

> Tutoriel GitHub si vous n’êtes pas familier avec l’outil < (https://github.com/AresEnsea/2324_Projet2A_AresCFR/blob/main/Tutoriel%20Git/Tutoriel%20GitHub.pdf)

Sur GitHub, tous les fichiers relatifs aux sumobots y sont répertoriés, vous pourriez regarder comment ils ont été programmés, quels sont les composants qui figurent sur le PCB avec leurs valeurs associés, et bien d’autres choses encore !

choses !

Dès que vous avez réussi, amusez-vous à « tripatouiller le code » : prenez une carte Arduino Nano vierge et modifiez le code pour que le sumobot bouge sans communication Bluetooth, ou au bout de 10 secondes ; testez plein de

# Le microcontrôleur


### Pour ce composant deux écoles s’offrent à vous :


Arduino : Simple, rapide, efficace, on pourrait presque dire que c’est le « Scratch » de la programmation embarquée. Si vous débutez, ce sera votre compagnon idéal.

STM32 : La version hardcore. Il permet d’explorer davantage de possibilités avec les fonctionnalités qu’il offre, mais il nécessite aussi beaucoup (beaucoup) plus de technique qu’Arduino (configuration des broches dans l’ioc) et une maîtrise de concepts que vous n’apprendrez qu’en deuxième année (configuration de Timers, gestion d’interruptions). Je ne le conseille pas, mais si vous voulez, vous pouvez quand même essayer et faire un groupe pour donner un coup de main à une 3ème

année
qui bosse déjà dessus.

# Liste non exhaustive des composants à regarder

essayer d’autres idées également.

Les moteurs et les drivers : Essayez de contrôler un moteur DC en le commandant avec un pont en H ou un hacheur 4 cadrans, vous pouvez

dans les autres !

L’alimentation : Attention il y’a des instructions précises qui sont écrites dans le règlement de la coupe, n’oubliez pas d’y jeter un œil pour bien choisir.

Le système de détection : Parce que c’est mieux quand le robot ne fonce pas

au poids max !).

Une bonne pratique est d’essayer de faire fonctionner les composants que vous voulez utiliser une fois ou deux, pour voir comment ils se contrôlent.

Le bouton d’arrêt d’urgence : Facile à trouver, mais il faut quand même l’acheter donc dès que vous en trouvez un, parlez-en à la trésorière.

La mécanique du robot (Vous pensiez pouvoir y échapper ?) : Il faut penser à faire le châssis de votre PAMI en 3D pour qu’il puisse être imprimé. Cette partie implique que vous connaissez déjà la taille de votre PCB. Pensez aussi aux choix des roues qui ne doivent pas trop déraper sur le vinyle (Attention

La gestion du démarrage du robot via une tirette : Plusieurs méthodes sont possibles, n’hésitez pas à voir ce qui est fait sur le Discord de la Coupe.

# Si les idées vous manquent

# Les liens utiles

Discord d’Ares; Discord Coupe de France de Robotique; Wiki d’Ares; Github du Projet CFR 2024

# Bon courage et amusez-vous bien !

# FIN

Demandez aux membres du bureau ! Ils sont pas mal occupés avec le robot principal, mais y’en a aucun qui mord, donc ils vous donneront des conseils ou un coup de main volontiers. Vous pouvez aussi demander conseil aux professeurs qui encadrent le projet de 2ème année (Nicolas PAPAZOGLOU & Laurent FIACK), à Patricia KITTEL, ou encore aux anciens membres d’Ares sur le Discord de l’asso. Vous pouvez également utiliser le Discord officiel de la coupe pour poser des questions à toutes les équipes qui y sont. Elles peuvent vous donner des pistes ou de l’inspiration.

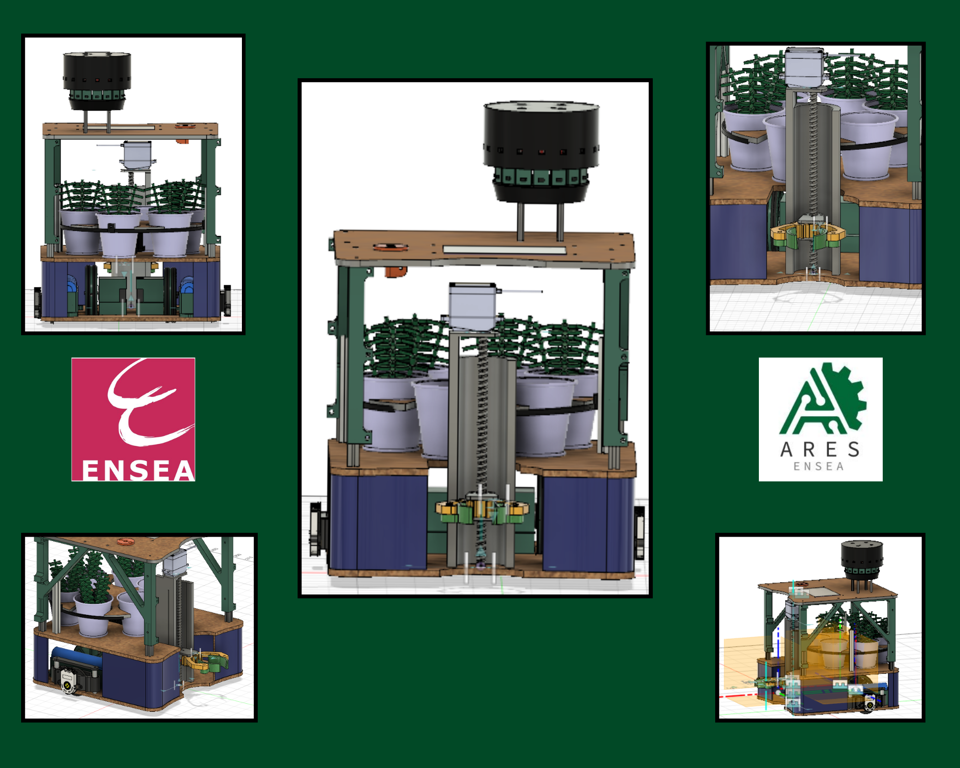
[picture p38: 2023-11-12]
2A/Mécanique/CAO/Photos/Beige minimalist photo collage (1).png

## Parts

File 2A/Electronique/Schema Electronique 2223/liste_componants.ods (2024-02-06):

Source:
Date: | 30/01/2024 17:35:17
Tool: | Eeschema 7.0.10
Generator:
Component Count: | 82
Collated Components:
Item | Qty | Reference(s) | Value | LibPart | Footprint | Datasheet | DNP | Farnell | MFR | MPN | Vmax
1 | 1 | C101 | 10u | Device:C_Polarized_Small | Capacitor_SMD:CP_Elec_4x5.4 | https://www.we-online.com/components/products/datasheet/865060440001.pdf |  |  |  | 8,6506E+11 | 25V
2 | 6 | C201, C401, C501, C701, C901, C903 | 100n | Device:C_Small | Capacitor_SMD:C_0402_1005Metric | ~
3 | 2 | C301, C601 | 100u | Device:C_Polarized | Capacitor_SMD:CP_Elec_6.3x7.7 | https://www.we-online.com/components/products/datasheet/865060445005.pdf |  |  |  | 8,6506E+11 | 25V
4 | 4 | C302, C303, C602, C603 | 10n | Device:C_Small | Capacitor_SMD:C_0402_1005Metric | ~
5 | 4 | C304, C305, C604, C605 | 22u | Device:C_Polarized_Small | Capacitor_SMD:CP_Elec_4x5.4 | https://www.we-online.com/components/products/datasheet/865060240001.pdf |  |  | 8,6506E+11 |  | 10V
6 | 1 | C902 | 100u | Device:C_Polarized_Small | Capacitor_SMD:CP_Elec_6.3x7.7 | ~ |  |  |  | 8,6506E+11 | 25V
7 | 1 | D101 | TVS 20.5V | Diode:1.5KExxCA | Diode_SMD:D_SMB | https://www.st.com/resource/en/datasheet/sm6t24a.pdf |  |  |  | SM6T24A
8 | 4 | D102, D103, D104, D105 | LED | Device:LED | LED_SMD:LED_0603_1608Metric | ~
9 | 2 | D301, D601 | D_Schottky | Device:D_Schottky | custom:DST10100S | https://www.mouser.fr/datasheet/2/240/media-3323546.pdf |  |  |  | DST10100S
10 | 4 | H101, H102, H103, H104 | MountingHole_Pad | Mechanical:MountingHole_Pad | MountingHole:MountingHole_2.7mm_M2.5_Pad_Via | ~
11 | 1 | J101 | Bat 2 | Connector_Generic:Conn_01x02 | custom:691322110002 | https://www.we-online.com/components/products/datasheet/691322110002.pdf |  |  |  | 6,91322E+11
12 | 1 | J102 | Bat 1 | Connector_Generic:Conn_01x02 | custom:691322110002 | https://www.we-online.com/components/products/datasheet/691322110002.pdf |  |  |  | 6,91322E+11
13 | 1 | J103 | AU | Connector_Generic:Conn_01x02 | custom:691322110002 | https://www.we-online.com/components/products/datasheet/691322110002.pdf |  |  |  | 6,91322E+11
14 | 1 | J104 | Switch | Connector_Generic:Conn_01x02 | custom:691322110002 | https://www.we-online.com/components/products/datasheet/691322110002.pdf |  |  |  | 6,91322E+11
15 | 1 | J105 | Conn_RPI | Connector_Generic:Conn_02x20_Odd_Even | Connector_PinSocket_2.54mm:PinSocket_2x20_P2.54mm_Vertical | ~
16 | 1 | J106 | Conn_Phidget_PS_Stepper_1 | Connector_Generic:Conn_01x02 | Connector_JST:JST_XH_B2B-XH-A_1x02_P2.50mm_Vertical | ~
17 | 1 | J107 | Conn_Phidget_PS_Stepper_2 | Connector_Generic:Conn_01x02 | Connector_JST:JST_XH_B2B-XH-A_1x02_P2.50mm_Vertical | ~
18 | 1 | J108 | Conn_Phidget_PS_Stepper_3 | Connector_Generic:Conn_01x02 | Connector_JST:JST_XH_B2B-XH-A_1x02_P2.50mm_Vertical | ~
19 | 1 | J109 | Conn_Phidget_PS_Stepper_4 | Connector_Generic:Conn_01x02 | Connector_JST:JST_XH_B2B-XH-A_1x02_P2.50mm_Vertical | ~
20 | 1 | J110 | Conn_01x02 | Connector_Generic:Conn_01x02 | Connector_JST:JST_XH_B2B-XH-A_1x02_P2.50mm_Vertical | ~
21 | 1 | J111 | Conn_GND | Connector_Generic:Conn_01x08 | Connector_PinHeader_2.54mm:PinHeader_1x08_P2.54mm_Vertical | ~
22 | 1 | J112 | Conn_GPIO_unused | Connector_Generic:Conn_01x08 | Connector_PinHeader_2.54mm:PinHeader_1x08_P2.54mm_Vertical | ~
23 | 1 | J113 | Conn_3.3V | Connector_Generic:Conn_01x08 | Connector_PinHeader_2.54mm:PinHeader_1x08_P2.54mm_Vertical | ~
24 | 2 | J114, J115 | Conn_01x05 | Connector_Generic:Conn_01x05 | Connector_JST:JST_XH_B5B-XH-A_1x05_P2.50mm_Vertical | ~
25 | 4 | J201, J401, J501, J701 | Conn_FDC | Connector_Generic:Conn_01x02 | Connector_JST:JST_XH_B2B-XH-A_1x02_P2.50mm_Vertical | ~
26 | 3 | J801, J1001, J1101 | Conn_UART | Connector_Generic:Conn_01x04 | Connector_JST:JST_XH_B4B-XH-A_1x04_P2.50mm_Vertical | ~
27 | 1 | J901 | Conn_XL320 | Connector_Generic:Conn_01x03 | Connector_JST:JST_XH_B3B-XH-A_1x03_P2.50mm_Vertical | ~
28 | 2 | L301, L601 | 22m | Device:L_Small | Inductor_SMD:L_Changjiang_FNR8065S | ~ |  |  | 7447709220
29 | 1 | R101 | 4k7 | Device:R_Small | Resistor_SMD:R_0402_1005Metric | ~
30 | 1 | R102 | 1k8 | Device:R_Small | Resistor_SMD:R_0402_1005Metric | ~
31 | 6 | R103, R104, R202, R402, R502, R702 | 1k | Device:R_Small | Resistor_SMD:R_0402_1005Metric | ~
32 | 4 | R201, R401, R501, R701 | 100k | Device:R_Small | Resistor_SMD:R_0402_1005Metric | ~
33 | 2 | R301, R601 | 2.7k | Device:R_Small | Resistor_SMD:R_0402_1005Metric | ~
34 | 2 | R302, R602 | 2k87 | Device:R_Small | Resistor_SMD:R_0402_1005Metric | ~
35 | 2 | R303, R603 | 2k2 | Device:R_Small | Resistor_SMD:R_0402_1005Metric | ~
36 | 3 | R901, R902, R903 | 10k | Device:R_Small | Resistor_SMD:R_0402_1005Metric | ~
37 | 1 | TP101 | TestPoint | Connector:TestPoint | Connector_Pin:Pin_D0.9mm_L10.0mm_W2.4mm_FlatFork | ~
38 | 1 | TP102 | 5.1V | Connector:TestPoint | Connector_Pin:Pin_D0.9mm_L10.0mm_W2.4mm_FlatFork | ~
39 | 1 | TP103 | 7.4V | Connector:TestPoint | Connector_Pin:Pin_D0.9mm_L10.0mm_W2.4mm_FlatFork | ~
40 | 1 | TP104 | 3V3 | Connector:TestPoint | Connector_Pin:Pin_D0.9mm_L10.0mm_W2.4mm_FlatFork | ~
41 | 2 | U301, U601 | LT1076CR-PBF | :LT1076_1 | Package_TO_SOT_SMD:TO-263-7_TabPin4 | https://www.mouser.fr/datasheet/2/609/1074fds-3123169.pdf
42 | 1 | U901 | 74LVC2G241 | 74xGxx:74LVC2G241 | Package_SO:VSSOP-8_2.3x2mm_P0.5mm | https://4donline.ihs.com/images/VipMasterIC/IC/PHGL/PHGLS27073/PHGLS27073-1.pdf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 |  | https://fr.farnell.com/nexperia/74lvc2g241dc-125/buffer-driver-de-ligne-40-a-125/dp/3442085?st=74LVC2G241DC,125
Nb composants : | 82
 |  | R302 | 3k52
 |  | R303 | 1k5 | resistance pour les bucks

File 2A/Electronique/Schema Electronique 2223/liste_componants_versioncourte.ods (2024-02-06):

null | Sourced | Placed | References | Value | Footprint | Quantity
1 |  |  | C201, C401, C501, C701, C901, C903 | 100n | C_0402_1005Metric | 6
2 |  |  | C302, C303, C602, C603 | 10n | C_0402_1005Metric | 4
3 |  |  | C304, C305, C604, C605 | 22u | CP_Elec_4x5.4 | 4
4 |  |  | C301, C601, C902 | 100u | CP_Elec_6.3x7.7 | 3
5 |  |  | C101 | 10u | CP_Elec_4x5.4 | 1
6 |  |  | R103, R104, R202, R402, R502, R702 | 1k | R_0402_1005Metric | 6
7 |  |  | R201, R401, R501, R701 | 100k | R_0402_1005Metric | 4
8 |  |  | R901, R902, R903 | 10k | R_0402_1005Metric | 3
9 |  |  | R301, R601 | 2.7k | R_0402_1005Metric | 2
10 |  |  | R302, R602 | 2k87 | R_0402_1005Metric | 2
11 |  |  | R303, R603 | 2k2 | R_0402_1005Metric | 2
12 |  |  | R101 | 4k7 | R_0402_1005Metric | 1
13 |  |  | R102 | 1k8 | R_0402_1005Metric | 1
14 |  |  | L301, L601 | 22m | L_Changjiang_FNR8065S | 2
15 |  |  | D102, D103, D104, D105 | LED | LED_0603_1608Metric | 4
16 |  |  | D301, D601 | D_Schottky | DST10100S | 2
17 |  |  | D101 | TVS 20.5V | D_SMB | 1
18 |  |  | U301, U601 | LT1076CR-PBF | TO-263-7_TabPin4 | 2
19 |  |  | U901 | 74LVC2G241 | VSSOP-8_2.3x2mm_P0.5mm | 1
20 |  |  | H101, H102, H103, H104 | MountingHole_Pad | MountingHole_2.7mm_M2.5_Pad_Via | 4
21 |  |  | TP101 | TestPoint | Pin_D0.9mm_L10.0mm_W2.4mm_FlatFork | 1
22 |  |  | TP102 | 5.1V | Pin_D0.9mm_L10.0mm_W2.4mm_FlatFork | 1
23 |  |  | TP103 | 7.4V | Pin_D0.9mm_L10.0mm_W2.4mm_FlatFork | 1
24 |  |  | TP104 | 3V3 | Pin_D0.9mm_L10.0mm_W2.4mm_FlatFork | 1
25 |  |  | J201, J401, J501, J701 | Conn_FDC | JST_XH_B2B-XH-A_1x02_P2.50mm_Vertical | 4
26 |  |  | J801, J1001, J1101 | Conn_UART | JST_XH_B4B-XH-A_1x04_P2.50mm_Vertical | 3
27 |  |  | J114, J115 | Conn_01x05 | JST_XH_B5B-XH-A_1x05_P2.50mm_Vertical | 2
28 |  |  | J101 | Bat 2 | 691322110002 | 1
29 |  |  | J102 | Bat 1 | 691322110002 | 1
30 |  |  | J103 | AU | 691322110002 | 1
31 |  |  | J104 | Switch | 691322110002 | 1
32 |  |  | J105 | Conn_RPI | PinSocket_2x20_P2.54mm_Vertical | 1
33 |  |  | J106 | Conn_Phidget_PS_Stepper_1 | JST_XH_B2B-XH-A_1x02_P2.50mm_Vertical | 1
34 |  |  | J107 | Conn_Phidget_PS_Stepper_2 | JST_XH_B2B-XH-A_1x02_P2.50mm_Vertical | 1
35 |  |  | J108 | Conn_Phidget_PS_Stepper_3 | JST_XH_B2B-XH-A_1x02_P2.50mm_Vertical | 1
36 |  |  | J109 | Conn_Phidget_PS_Stepper_4 | JST_XH_B2B-XH-A_1x02_P2.50mm_Vertical | 1
37 |  |  | J110 | Conn_01x02 | JST_XH_B2B-XH-A_1x02_P2.50mm_Vertical | 1
38 |  |  | J111 | Conn_GND | PinHeader_1x08_P2.54mm_Vertical | 1
39 |  |  | J112 | Conn_GPIO_unused | PinHeader_1x08_P2.54mm_Vertical | 1
40 |  |  | J113 | Conn_3.3V | PinHeader_1x08_P2.54mm_Vertical | 1
41 |  |  | J901 | Conn_XL320 | JST_XH_B3B-XH-A_1x03_P2.50mm_Vertical | 1
 |  |  |  |  |  | 82

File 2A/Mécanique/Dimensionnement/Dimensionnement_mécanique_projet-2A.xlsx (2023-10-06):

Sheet: Espace_stockage
TABLEAU DE DECISION POUR LA PARTIE MECANIQUE
NOM DE L’ÉQUIPE |  | ARES
ANNÉE |  | 2023-2024
ORGANISATION |  | ENSEA
EQUIPE MECANIQUE et ELECTRONIQUE |  |  | Adresse mail
Nathan Faget |  |  | nathan.faget@ensea.fr
Fannie Bichemin |  |  | fannie.bichemin@ensea.fr
EQUIPE INFORMATIQUE |  |  | Adresse mail
Ousmane Thiongane |  |  | ousmane.thiongane@ensea.fr
Rémi Weidle |  |  | remi.weidle@ensea.fr
ESPACE DE STOCKAGE
# | Critère | Dimensionnement (mm) / nombre | Argument / Explication | Avis consultant | Remarque extérieure
1 | Forme de la base de stockage
2 | Dimension de la base de stockage
3 | Epaisseur de la base de stockage
4 | Forme des espaces pour contenir les pots
5 | Dimension des espaces pour contenir les pots
6 | Fixation de l'espace de stockage
7 | Vis
8 | Trous pour assembler
9
10
11
12

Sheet: Pince_avant
TABLEAU DE DECISION POUR LA PARTIE MECANIQUE
NOM DE L’ÉQUIPE |  | ARES
ANNÉE |  | 2023-2024
ORGANISATION |  | ENSEA
EQUIPE MECANIQUE et ELECTRONIQUE |  |  | Adresse mail
Nathan Faget |  |  | nathan.faget@ensea.fr
Fannie Bichemin |  |  | fannie.bichemin@ensea.fr
EQUIPE INFORMATIQUE |  |  | Adresse mail
Ousmane Thiongane |  |  | ousmane.thiongane@ensea.fr
Rémi Weidle |  |  | remi.weidle@ensea.fr
PINCE AVANT
# | Critère | Dimensionnement (mm) / nombre | Argument / Explication | Avis consultant | Remarque extérieure
1 | Forme générale des pinces
2 | Longueur de chaque pince
3 | Epaisseur de chaque pince
4 | Vis
5 | Réunion des deux pinces
6 | Fixation de la pince sur l'ascenseur
7 | Forme de la fixation
8 | Taille de la fixation
9 | Diamètre de l'intérieur de la pince
10 | Forme du bout de la pince pour (aggriper les pots)
11 | Taille du bout de la pince pour (aggriper les pots)
12
13
14

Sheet: Ascenseur
 | TABLEAU DE DECISION POUR LA PARTIE MECANIQUE
 | NOM DE L’ÉQUIPE |  | ARES
 | ANNÉE |  | 2023-2024
 | ORGANISATION |  | ENSEA
 | EQUIPE MECANIQUE et ELECTRONIQUE |  |  | Adresse mail
 | Nathan Faget |  |  | nathan.faget@ensea.fr
 | Fannie Bichemin |  |  | fannie.bichemin@ensea.fr
 | EQUIPE INFORMATIQUE |  |  | Adresse mail
 | Ousmane Thiongane |  |  | ousmane.thiongane@ensea.fr
 | Rémi Weidle |  |  | remi.weidle@ensea.fr
 | Ascenceur
# | Critère | Dimensionnement (mm) / nombre | Argument / Explication | Avis consultant | Remarque extérieure
1 | Forme des rails
2 | Largeur des rails
3 | Longueur des railles
4 | Forme de la fixation au robot
5 | Largeur de la fixation
6 | Longeur de la fixation
7 | Epaisseur de la fixation
8
9
10
11
12

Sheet: Pince arrière
TABLEAU DE DECISION POUR LA PARTIE MECANIQUE
NOM DE L’ÉQUIPE |  | ARES
ANNÉE |  | 2023-2024
ORGANISATION |  | ENSEA
EQUIPE MECANIQUE et ELECTRONIQUE |  |  | Adresse mail
Nathan Faget |  |  | nathan.faget@ensea.fr
Fannie Bichemin |  |  | fannie.bichemin@ensea.fr
EQUIPE INFORMATIQUE |  |  | Adresse mail
Ousmane Thiongane |  |  | ousmane.thiongane@ensea.fr
Rémi Weidle |  |  | remi.weidle@ensea.fr
0
PINCE ARRIERE
# | Critère | Dimensionnement (mm) / nombre | Argument / Explication | Avis consultant | Remarque extérieure
1
2
3
4
5
6
7
8
9
10
11
12

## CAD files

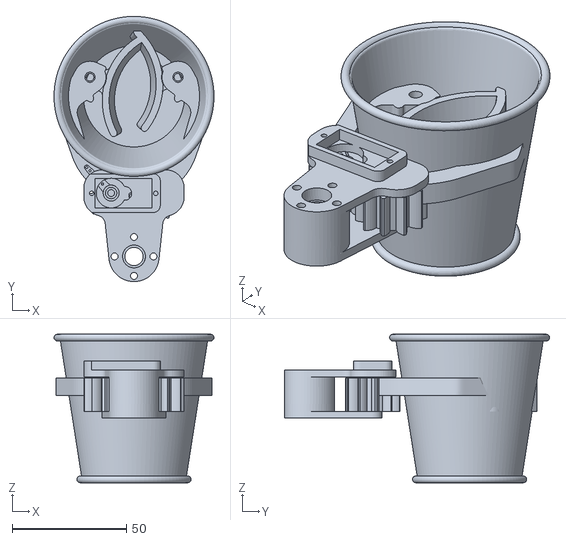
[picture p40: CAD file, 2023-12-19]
2A/Mécanique/CAO/fichier stl/Assemblage_Pince_V2 v46.stl
70.0 x 116.0 x 65.0

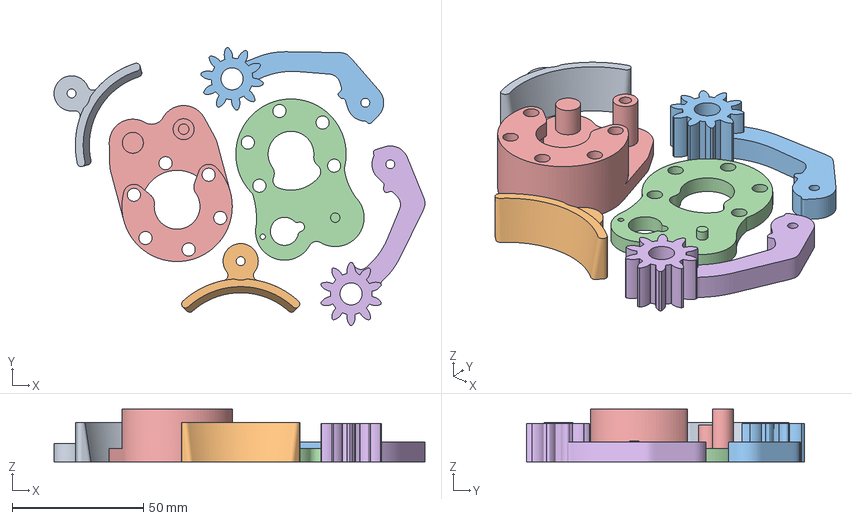
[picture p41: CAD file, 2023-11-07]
2A/Mécanique/CAO/fichier stl/ascenseur/pince/montage_total.3mf
141.2 x 105.7 x 20.0 mm
cercle_droit.stl
cercle_gauche.stl
bras_droit.stl
couvercle.stl
base.stl
bras_gauche.stl

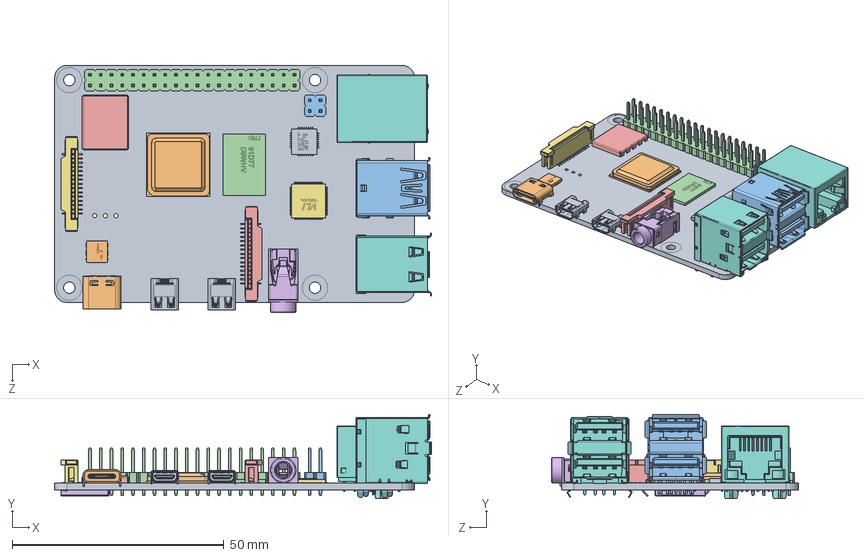
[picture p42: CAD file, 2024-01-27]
2A/Mécanique/CAO/Fichier/piece téléchargé/raspberry-pi-4-model-b-1.snapshot.3/Raspberry Pi 4 Model B.SLDASM
89.0 x 19.9 x 58.4 mm
PCB, RPi4ModelB
Broadcom BCM2711B0 CPU, RPi4ModelB
2.54 mm DUPONT MALE PIN HEADER, POE, 2X2, RPi4ModelB
2.54 mm DUPONT MALE PIN HEADER, IO, 2X20, RPi4ModelB
Camera Connector, RPi4ModelB
Microphone Plug, RPi4ModelB
Display Connector, RPi4ModelB
Gigabit Ethernet Port, RPi4ModelB
Female Micro HDMI Connector, RPi4ModelB x 2
Female USB Type C Connector, RPi4ModelB
2X USB3.0 PORTS, RPi4ModelB
91D77 D9WHV 778K, 4 GB LPDDR4 SDRAM, RPi4ModelB
Cypress CYW43455 Wireless Module Cover, RPi4ModelB
SD Card Slot, RPi4ModelB
VIA VL805 PCIe USB 3.0 controller, RPi4ModelB
2X USB2.0 PORTS, RPi4ModelB
Broadcom BCM54213PE Gigabit Ethernet Transceiver, RPi4ModelB
MxL7704 Universal PMIC, RPi4ModelB

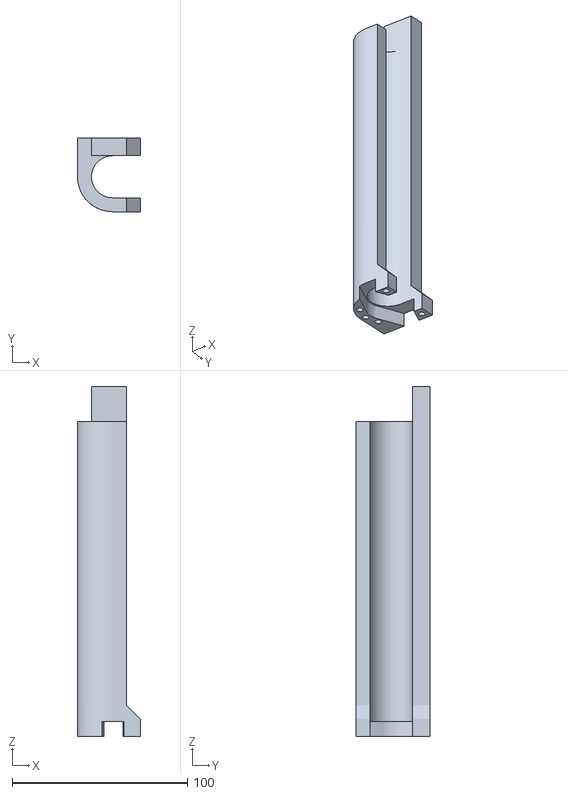
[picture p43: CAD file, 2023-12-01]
2A/Mécanique/CAO/fichier stl/ascenseur/Corps_ascenseur.stl
36.0 x 42.0 x 200.0

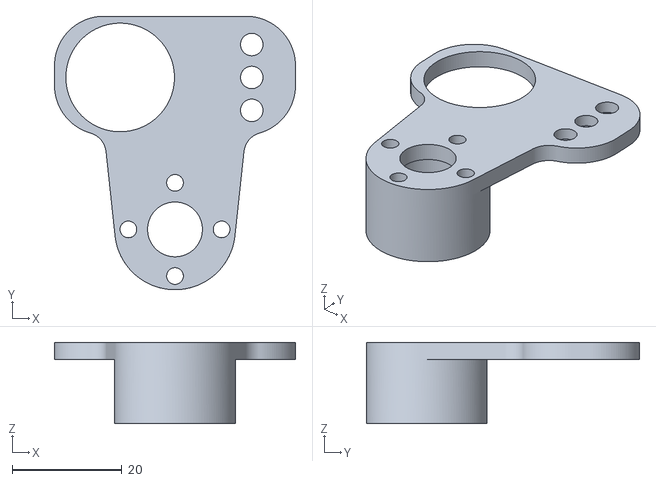
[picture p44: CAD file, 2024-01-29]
2A/Mécanique/CAO/fichier stl/ascenseur/pince/dessuspince.stl
44.0 x 49.9 x 14.8

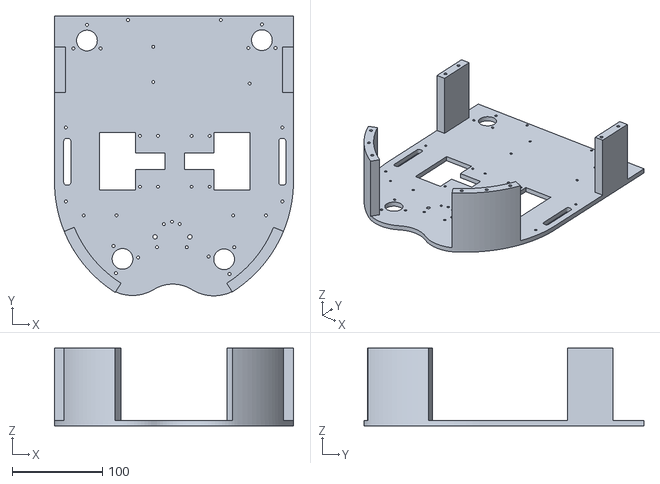
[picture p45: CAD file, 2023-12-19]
2A/Mécanique/CAO/fichier stl/Base_V2 v84.stl
265.0 x 310.1 x 86.0

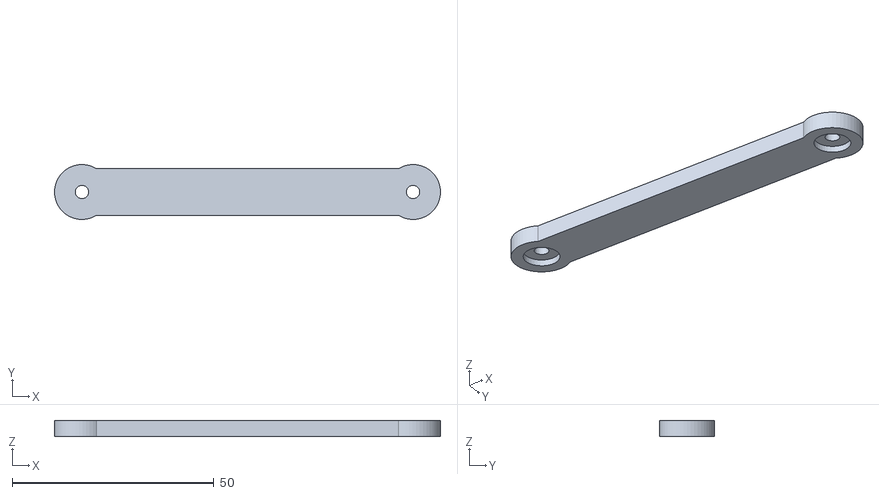
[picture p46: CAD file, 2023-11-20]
2A/Mécanique/CAO/fichier stl/robot/odometrie/dessus.stl
95.6 x 13.6 x 4.00

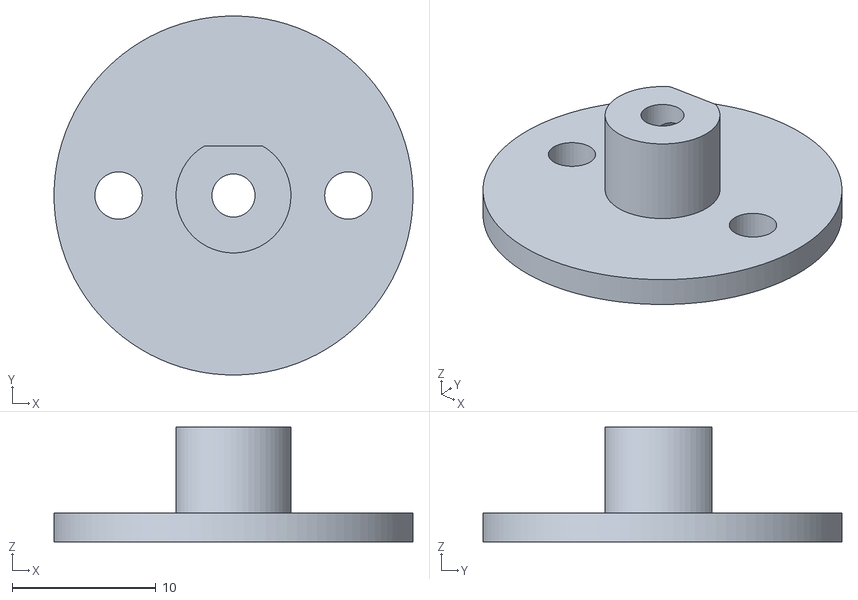
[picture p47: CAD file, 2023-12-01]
2A/Mécanique/CAO/fichier stl/robot/raccordstepper.stl
25.0 x 25.0 x 8.00

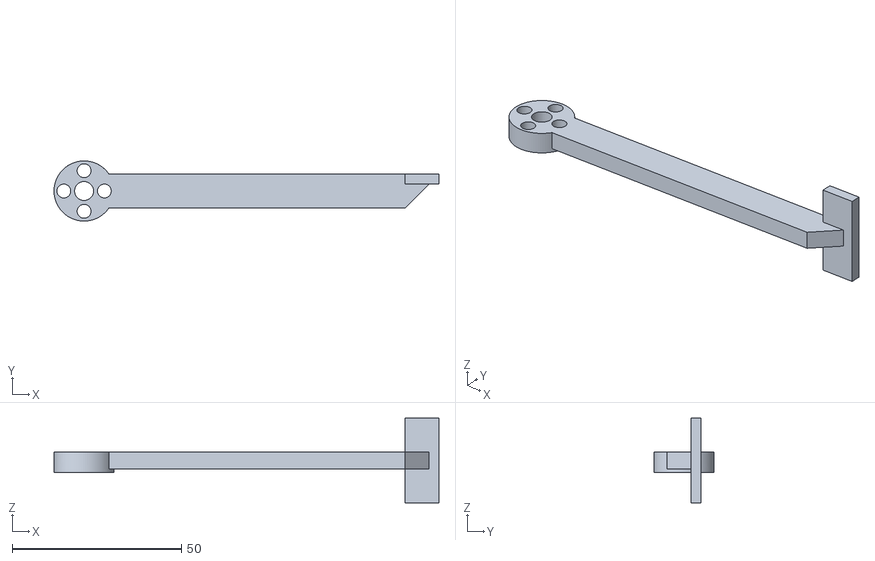
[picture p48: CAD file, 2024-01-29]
2A/Mécanique/CAO/fichier stl/robot/stockage/pousse_pot.stl
113.9 x 17.8 x 25.0

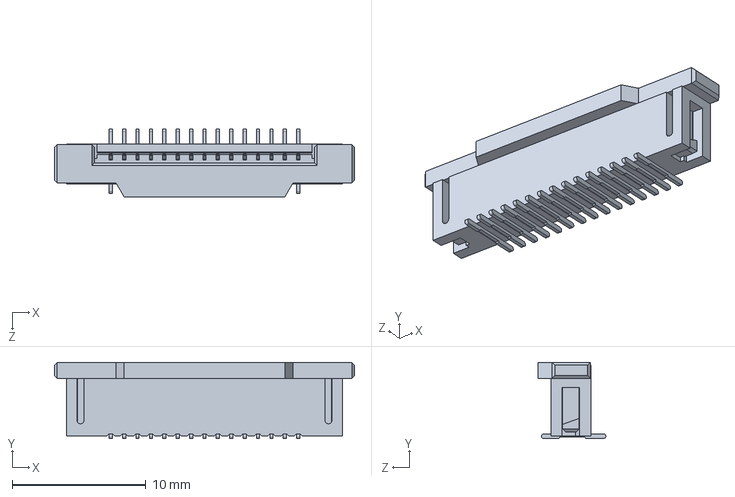
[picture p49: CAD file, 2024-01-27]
2A/Mécanique/CAO/Fichier/piece téléchargé/raspberry-pi-4-model-b-1.snapshot.3/Camera Connector, RPi4ModelB.SLDPRT
22.4 x 5.68 x 5.07 mm

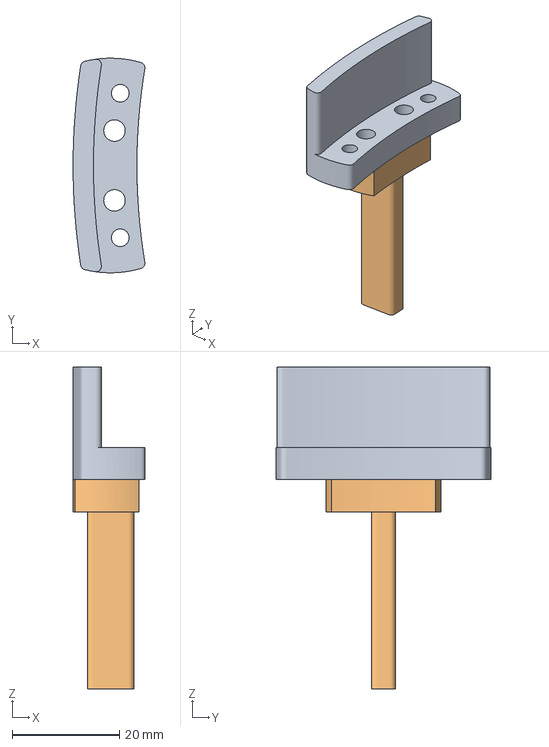
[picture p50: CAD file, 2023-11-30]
2A/Mécanique/CAO/Fichier_3mf/Support_bord_symétrie v1.3mf
13.4 x 40.0 x 60.0 mm
Corps1 x 2

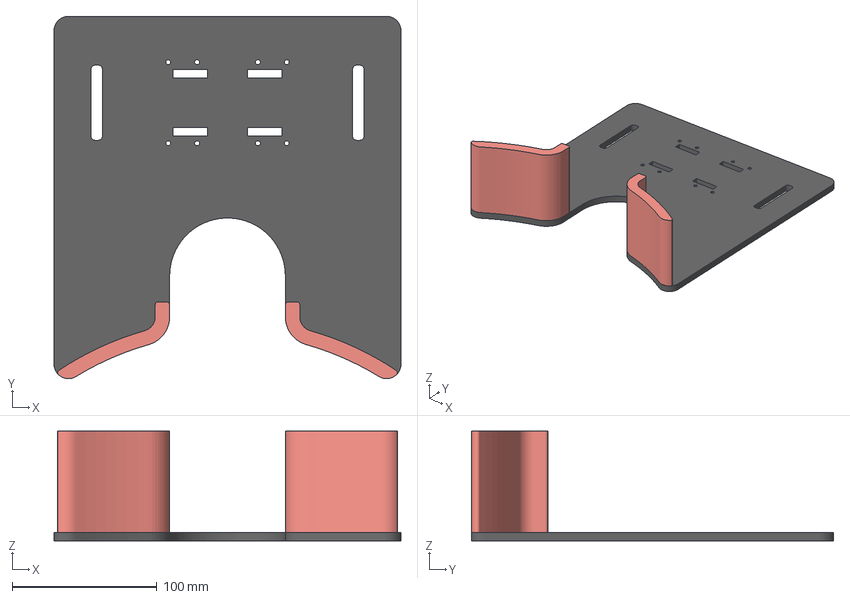
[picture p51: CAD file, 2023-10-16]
2A/Mécanique/CAO/Photos/Partie_Haute_Plastique v10.3mf
240.0 x 250.6 x 76.0 mm
Corps2
Corps3

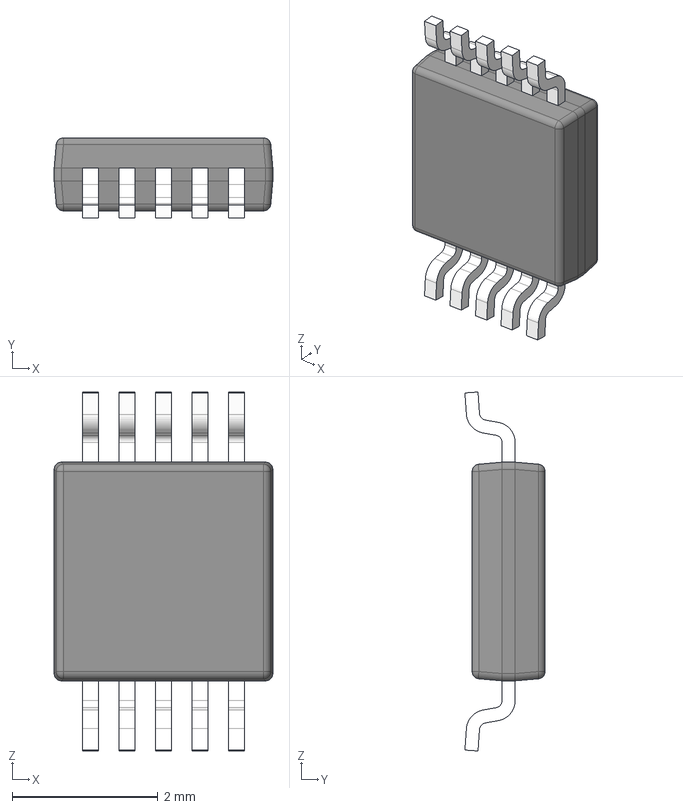
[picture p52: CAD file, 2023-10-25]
3A/load/DAC7811IDGST/DAC7811IDGST.stp
3.00 x 1.10 x 4.93 mm
BODY-SO
LEAD-SO x 10
PIN1-ID

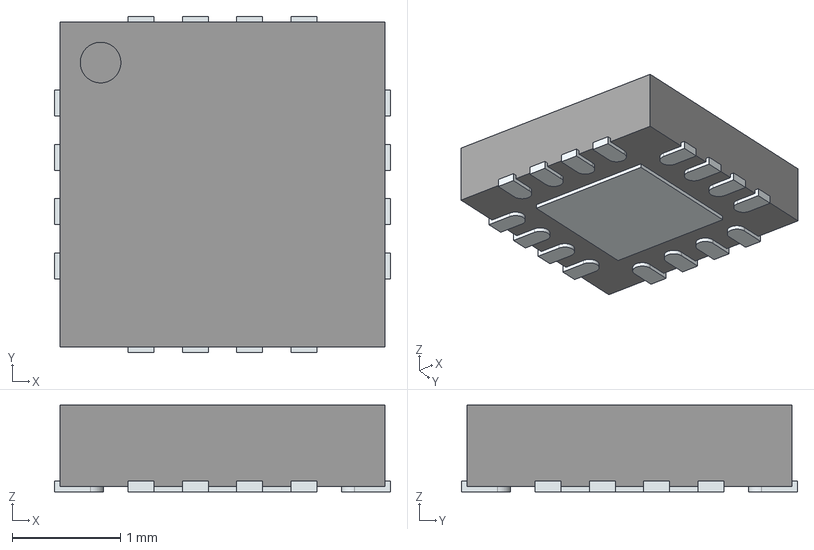
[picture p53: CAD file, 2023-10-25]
3A/load/TLA2518/TLA2518IRTER.stp
3.10 x 3.10 x 0.8 mm
ThermalPin
PinsArrayLR
PinsArrayTB

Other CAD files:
2A/Mécanique/CAO/fichier stl/ascenseur/pince/bras_gauche.stl
2A/Mécanique/CAO/fichier stl/ascenseur/support_moteur.stl
2A/Mécanique/CAO/fichier stl/robot/odometrie/oddo part2.stl
2A/Mécanique/CAO/fichier stl/robot/rabat pot 2.stl
2A/Mécanique/CAO/Fichier/Base_Robot.f3d
2A/Mécanique/CAO/Fichier/Partie_Haute_Plastique.f3z
2A/Mécanique/CAO/Fichier/piece téléchargé/7447709001_Download_WE-PD_1210_STP_rev1.stp
2A/Mécanique/CAO/Fichier/piece téléchargé/ACOPLE EJE 8 mm a 5 mm.stl
2A/Mécanique/CAO/Fichier/piece téléchargé/Makerbeam_Glissiere_Rail_Lineair v1 v1.f3d
2A/Mécanique/CAO/Fichier/piece téléchargé/Makerbeam_Rail_Lineair_200mm v1 v1.f3d
2A/Mécanique/CAO/Fichier/piece téléchargé/Makerbeam_Rail_Lineair_300mm v1 v1.f3d
2A/Mécanique/CAO/Fichier/piece téléchargé/Nema17_25mm v1 v1.f3d
2A/Mécanique/CAO/Fichier/piece téléchargé/XL-320.step
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

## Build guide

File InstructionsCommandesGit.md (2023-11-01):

### Lire le fichier "Tutoriel GitHub.pdf" pour savoir comment utiliser ces commandes.

/!\ Si vous n'êtes pas contribueur principal, ces actions sont à réaliser sur votre fork /!\

La première étape (met à jour les dossiers en fonction de ceux sur le serveur) :

```
git pull
```

Pour ajouter des changements : 

```
git add * 
git commit -m "Commentaire sur la modification apportée"
git push
```

Pour supprimer des fichiers (par exemple un txt) :

```
git rm "Nom du fichier.txt"
git commit -m "Commentaire sur la modification apportée"
git push
```
Pensez à faire des "pull request".

Guides des commandes :

Pour avoir plus d'informations sur comment utiliser GitHub :	

- https://www.hostinger.fr/tutoriels/commandes-git#Git_config

- https://www.youtube.com/watch?v=gp_k0UVOYMw

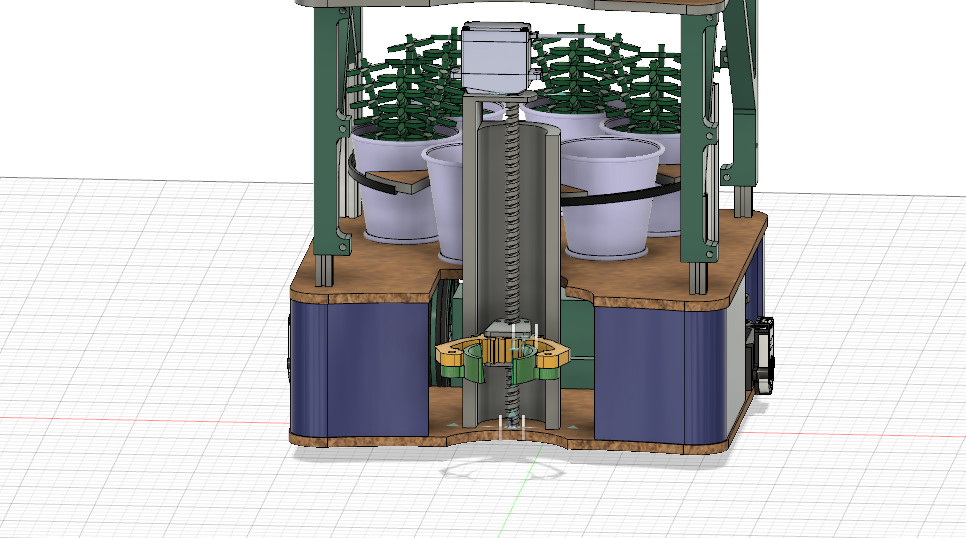
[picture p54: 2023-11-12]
2A/Mécanique/CAO/Photos/assemblage_23-24 v39.png

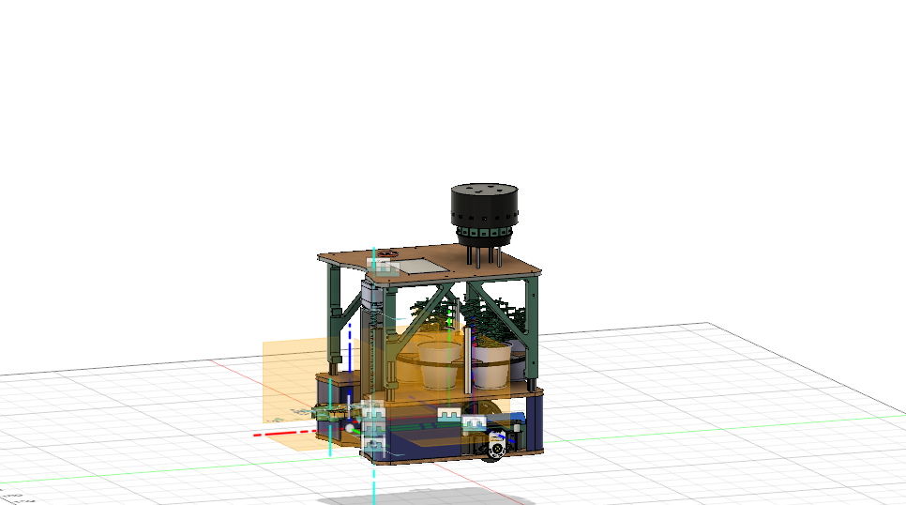
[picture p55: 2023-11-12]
2A/Mécanique/CAO/Photos/assemblage_23-24 v38.png

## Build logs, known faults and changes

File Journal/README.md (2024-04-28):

# Journal de Bord d'Ares 
Ce dossier constitue le journal de bord d'Ares, retraçant les réalisations hebdomadaires de l'association.

## Tutoriels
Tous les tutoriels et les méthodes de réalisations concernant la Coupe de France de Robotique 2024 sont regroupés sur le wiki de l'association : https://wiki.ares.asso-ensea.fr/index.php/Coupe_de_France_de_Robotique

## Résumés Hebdomadaires 
### Mardi 19 Septembre (J-232)
- Disscussions et réflexions autour du projet
- Répartition des tâches
- Élaboration de la présentation du projet

### Mardi 26 Septembre (J-225)
- Présentation du projet, des solutions envisagées et de la stratégie. Réflexion sur le diagramme d'architecture
- Installation de ROS2 et réalisation du tutoriel
- Inscription d'Ares à la Coupe de France de Robotique
- Rédaction de la démarche sur le wiki : https://wiki.ares.asso-ensea.fr/index.php/Introduction_%C3%A0_ROS_2
- Rédaction du tutoriel d'utilisation de GitHub pour les premières années (voir "Tutoriel GitHub.pdf" à la racine du repository)

### Mardi 3 octobre (J-218)
- Poursuite de l'apprentissage de ROS2, assimilation des différentes notions (Nodes, topics, services, actions)
- Étude du fonctionnement de l'écran STM32F746 Discovery
- Rédaction du cahier des charges de la statégie d'évitement : Méthode des Points de Sûreté (MPDS)
- Création de l'architecture du système : fichier conçu sur l'outil drawio (fichier architecture.drawio). Réflexion concernant les composants à utiliser, comparaison entre différents paramètres
- Résolution du problème mécanique. Description de la solution dans le readme principal (2 pinces, un ascenseur, un espace de stockage)

### Mardi 10 octobre (J-211)
- Élaboration de la machine à états de la MPDS
- Observations sur le fonctionnement du lidar TOF
- Étude du code pour le simulateur : Correction de la superposition entre la grille et l'image de la table de jeu, dont le décalage rendait les coordonnées fausses
- Elaboration plus précise de la stratégie mécanique
- Amélioration de l'architecture du système : création de la partie asservissement (ramassage et lâchage des objets)
- Création des conceptions 3D des pièces mécaniuques (les 2 pinces ainsi que l'ascenseur et la base du robot)
- Création de l'organigramme des packages ROS2, étude du Hardware pour le Robot ROS2 avec des phidgets.
- Commande des modules phidgets et découverte des librairies associés. 

### Mardi 17 octobre (J-204)
- Intégration du simulateur au site web de l'association afin de le rendre accessible à tous + correction mineure de l'exportation du code C
- Présentation de projet n°2 : Logigramme d'asservissement et diagrammes d'architecture du Robot, ROS 2 et logicielle
- Début de création de l'IHM pour la MPDS : UI réalisée avec PyQt3
- Finalisation des choix de dimensions pour les pièces mécaniques
- Recherches au sujet des capteurs de couleurs
- Ajout sur le wiki du tutoriel pour calibrer l'odométrie du robot : https://wiki.ares.asso-ensea.fr/index.php/Robot_STM32_%E2%80%93_Calibration_de_l%27odom%C3%A9trie
- Réalisation de la mécanique des roues + odométrie de Hugway. Ajout des modules phidgets, modélisation 3D des supports de codeurs et roue. 

### Mardi 24 octobre (J-197)
- Étude du code des années passées
- Installation de la nouvelle table
- Ajout de tutoriels et d'informations supplémentaires sur le wiki
- Démarrage de la rédaction du cahier des charges à donner aux premières années pour les PAMI
- Flash de la Raspberry avec docker
- Choix d'utiliser ROS2 Humble qui est supporté jusqu'en 2027 et connexion des modules phidgets aux composants de Ugway

### Mardi 7 novembre (J-183)
- Installation de ROS2 sur Ubuntu sur PC, prise en main de Gazebo, début de courbes avec phidgets desktop version...
- KiCad de la carte de puissance pour tout brancher à des batteries pour Hugway
- Correction du wiki avec l'ajout de ROS2 
- Création de la CAO de la pince avant du robot pour attraper les pots et les déposer sur la table ou dans les jardinières

### Mardi 14 novembre (J-176)
- Présentation de projet n°3 : CAO du Robot, refonte de la statégie d'évitement pour STM32, Avancement Robot Ugway (ROS2), Analyse des cartes électroniques
- Conversion de la stratégie d'évitement (Python -> C)
- Présentation de projet n°3 : CAO du Robot, refonte de la stratégie d'évitement pour STM32, Avancement Robot Ugway (ROS2), Analyse des cartes électroniques 

### Mardi 28 novembre (J-162)
- Création d'un package ROS2 pour les capteurs TOF VL53L1X
- Tentative de contact des ingénieurs d'Instar Robotics
- Essai de fonctionnement du moteur avec ROS2

### Mardi 5 décembre (J-155)
- Test de fonctionnement de la pince pour attraper les plantes
- Alimentaiton du wiki d'Ares - Comment faire fonctionner un signal PWM sur STM32 : https://wiki.ares.asso-ensea.fr/index.php/G%C3%A9n%C3%A9rer_des_signaux_PWM_avec_STM32_Cube_IDE

### Mardi 12 décembre (J-148)
- Test de fonctionnement des capteurs TOF en ROS2

### Lundi 25 décembre (J-135)
- Test de fonctionnement du capteur de couleur TCS3200 sous STM32

### Mardi 26 décembre (J-134)
- Calibration du capteur de couleur, finalisation du code
- Analyse du code de fonctionnement des roues motrices du robot
- Finalisation du code de la pince pour attraper les pots et les plantes

### Dimanche 31 Décembre (J-129)
- Rédaction du Dockerfile pour l'environnement ROS2
- Récupération du code de fonctionnement des capteurs TOF
- Rédaction du tutoriel (partie 1) sur l'installation de Docker sur Raspberry : https://wiki.ares.asso-ensea.fr/index.php/Introduction_%C3%A0_Docker#Mise_en_place_de_l%27environnement
- Rédaction du tutoriel (partie 2) sur les images et les conteneurs Docker : https://wiki.ares.asso-ensea.fr/index.php/Images_et_conteneurs

### Lundi 1 Janvier (J-128)
- Bonne année !
- Rédaction du tutoriel (partie 3) sur la création d'un Dockerfile : https://wiki.ares.asso-ensea.fr/index.php/Cr%C3%A9ation_d%27un_Dockerfile

### Vendredi 5 Janvier (J-124)
- Prise de contact avec l'ancien réalisateur du code du robot/simulateur
- Récupération du code de la première version du simulateur

### Vendredi 12 Janvier (J-117)
- Rendez-vous avec le réalisateur du code du robot/simulateur

### Mardi 16 Janvier (J-113)
- Présentation de projet n°4 : Récapitulatif des réalisations du semestre passé et plannification des missions pour les semaines à venir
- Étude de fonctionnement des servomoteurs Dynamixel XL-320

### Mardi 23 Janvier (J-106)
- Changement des pièces du robot pour s'adapter au XL-320
- Test du capteur de couleurs
- Réalisation du schématique de la carte mère
- Test des nouvelles pièces imprimées  

### Jeudi 25 Janvier (J-104)
- Paramétrisation de la Raspberry Pi 4
- Installation de Docker avec un image ROS2 Humble
- Recherche d'un package ROS2 pour faire fonctionner les Dynamixel

### Mardi 30 Janvier (J-99)
- Finalisation du pcb et commande des cartes et composants 
- Tests des nouvelles pièces 3D
- Implémentation de la deuxième partie de la stratégie d'évitement
- Test d'un capteur inductif pour la différenciation des pots métalliques
- Rédaction du code de fonctionnement des XL-320 (STM32)

### Mardi 6 Février (J-92)
- Présentation de projet n°5 : Présentation de la carte électronique de puissance, Mise à jour de la CAO, Actionneurs et Stratégie d'évitement, Avancement ROS2 et Dockerfiles

### Lundi 12 Février (J-86)
- Paramétrisation de la Raspberry Pi 4

### Mercredi 14 Février (J-84)
- Révision du code de fonctionnement des XL-320 (STM32)

### Mercredi 21 Février (J-77)
- Intégration du code des moteurs dans la Raspberry Pi 4

- ### Vendredi 23 Février (J-75)
- Test de micro-ros pour l'utilisation du lidar

### Mardi 27 Février (J-71)
- Rédaction d'un code Python permettant la gestion de la communication série
- Paramétrisation de la Raspberry Pi 4
- Ajout de la page wiki sur les bases de ROS2 : https://wiki.ares.asso-ensea.fr/index.php/Les_bases_de_ROS2 

### Mardi 5 Mars (J-64)
- Modification du code du lidar, tests du protocole 2 Dynamixel

### Mardi 12 Mars (J-57)
- Présentation de projet n°6 : Présentation de la carte électronique, avancement ROS2 et communication avec le lidar

### Dimanche 17 Mars (J-52)
- Réadaptation du code du lidar au format micro-ROS

### Mardi 19 Mars (J-50)
- Création du package de récupératioon des données du lidar
- Réédition du Dockerfile test pour ajouter les librairies nécessaires au fonctionnement du lidar 

### Mardi 26 Mars (J-43)
- Création du package de gestion du démarrage du robot (Écran de séléction de stratégie et démarrage à la tirette)

### Mardi 2 Avril (J-36)
- Présentation finale : Présentation de la Coupe de France de Robotique, du robot et de ses fonctionnalités
- Démonstration technique du robot

### Dimanche 7 Avril (J-31)
- Réécriture de la librairie pour les XL320 en Python

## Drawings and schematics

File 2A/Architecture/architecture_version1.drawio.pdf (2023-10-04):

## Alimentation Batterie

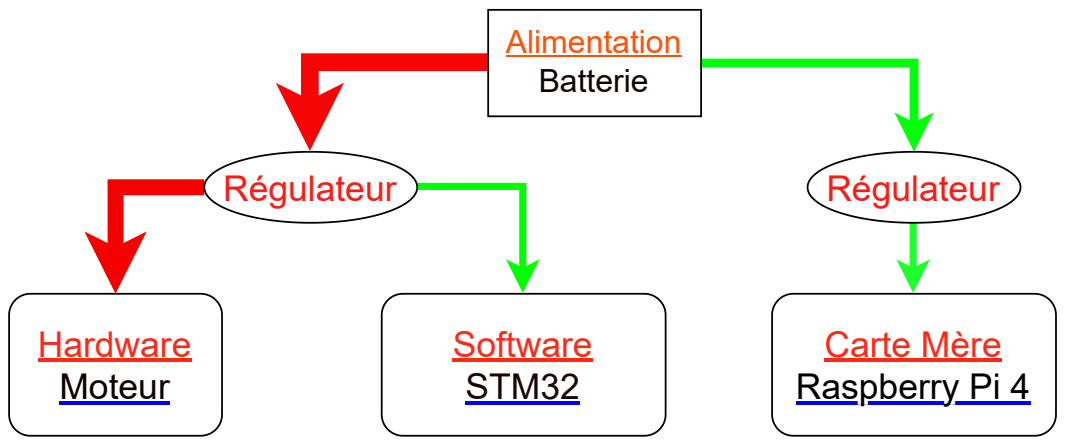
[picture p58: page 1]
Régulateur; Hardware Moteur; Software STM32; Carte Mère Raspberry Pi 4

## Moteurs

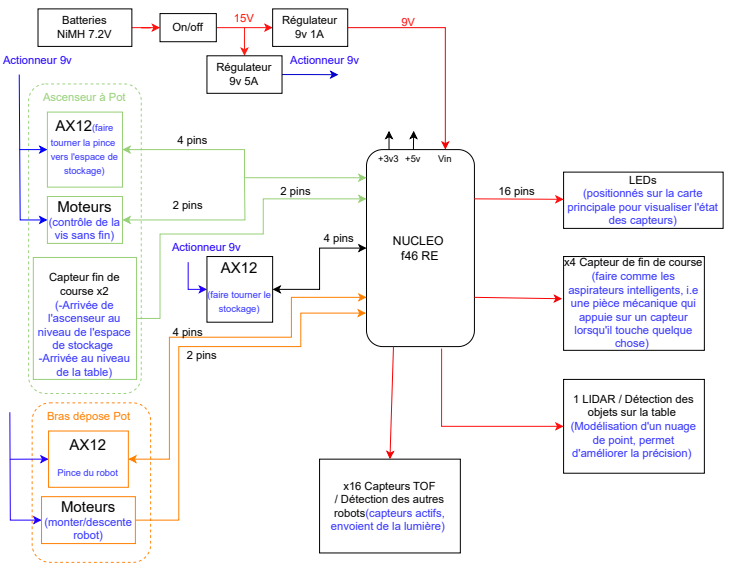
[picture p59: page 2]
AX12(faire; Ascenseur à Pot; NUCLEO f46 RE; Vin; Batteries; NiMH 7.2V; On/off; Régulateur 9v 1A; chose); LEDs; des capteurs); Régulateur 9v 5A; Actionneur 9v; 16 pins; 4 pins; 2 pins

tourner la pince
vers l'espace de
stockage)

(positionnés sur la carte
principale pour visualiser l'état

(contrôle de la
vis sans fin)

x4 Capteur de fin de course
(faire comme les
aspirateurs intelligents, i.e
une pièce mécanique qui
appuie sur un capteur
lorsqu'il touche quelque

Capteur fin de
course x2
(-Arrivée de
l'ascenseur au
niveau de l'espace
de stockage
-Arrivée au niveau
de la table)

(faire tourner le

1 LIDAR / Détection des
objets sur la table
(Modélisation d'un nuage
de point, permet
d'améliorer la précision)

Bras dépose Pot

Pince du robot
Moteurs
(monter/descente
robot)

x16 Capteurs TOF
/ Détection des autres
robots(capteurs actifs,
envoient de la lumière)

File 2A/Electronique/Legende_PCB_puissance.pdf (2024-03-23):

# Batterie

1

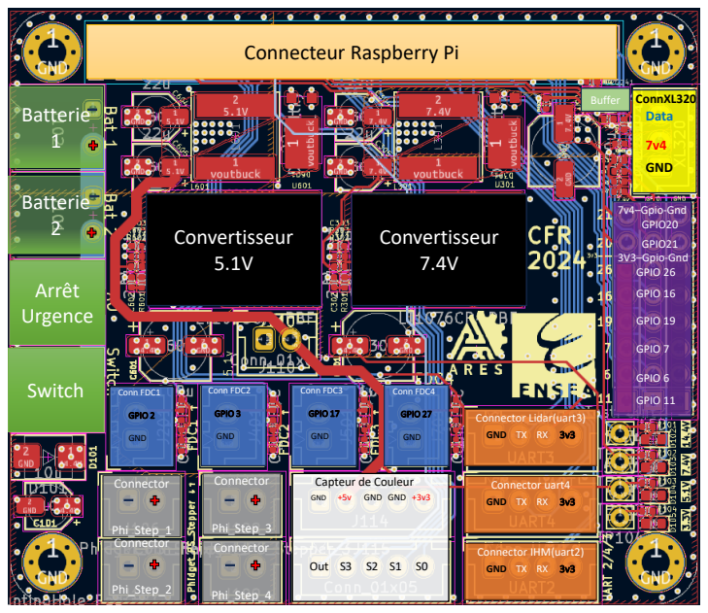
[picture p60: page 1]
Connector; Phi_Step_1; Phi_Step_3; Phi_Step_2; Phi_Step_4; GND; GND GND +3v3; Out S3 S2 S1 S0; Conn FDC1; GPIO 2; Batterie 2; Arrêt Urgence; Switch; ConnXL320 Data; Convertisseur 5.1V; Convertisseur 7.4V; Buffer; Conn FDC2; GPIO 3; Conn FDC3; GPIO 17; Conn FDC4; GPIO 27; 3V3–Gpio-Gnd GPIO 26; GPIO 16; GPIO 19; GPIO 7; GPIO 6; GPIO 11; 7v4–Gpio-Gnd GPIO20; GPIO21

Connecteur Raspberry Pi

Connector Lidar(uart3)
GND TX RX 3v3

Capteur de Couleur

Connector uart4

Connector IHM(uart2)

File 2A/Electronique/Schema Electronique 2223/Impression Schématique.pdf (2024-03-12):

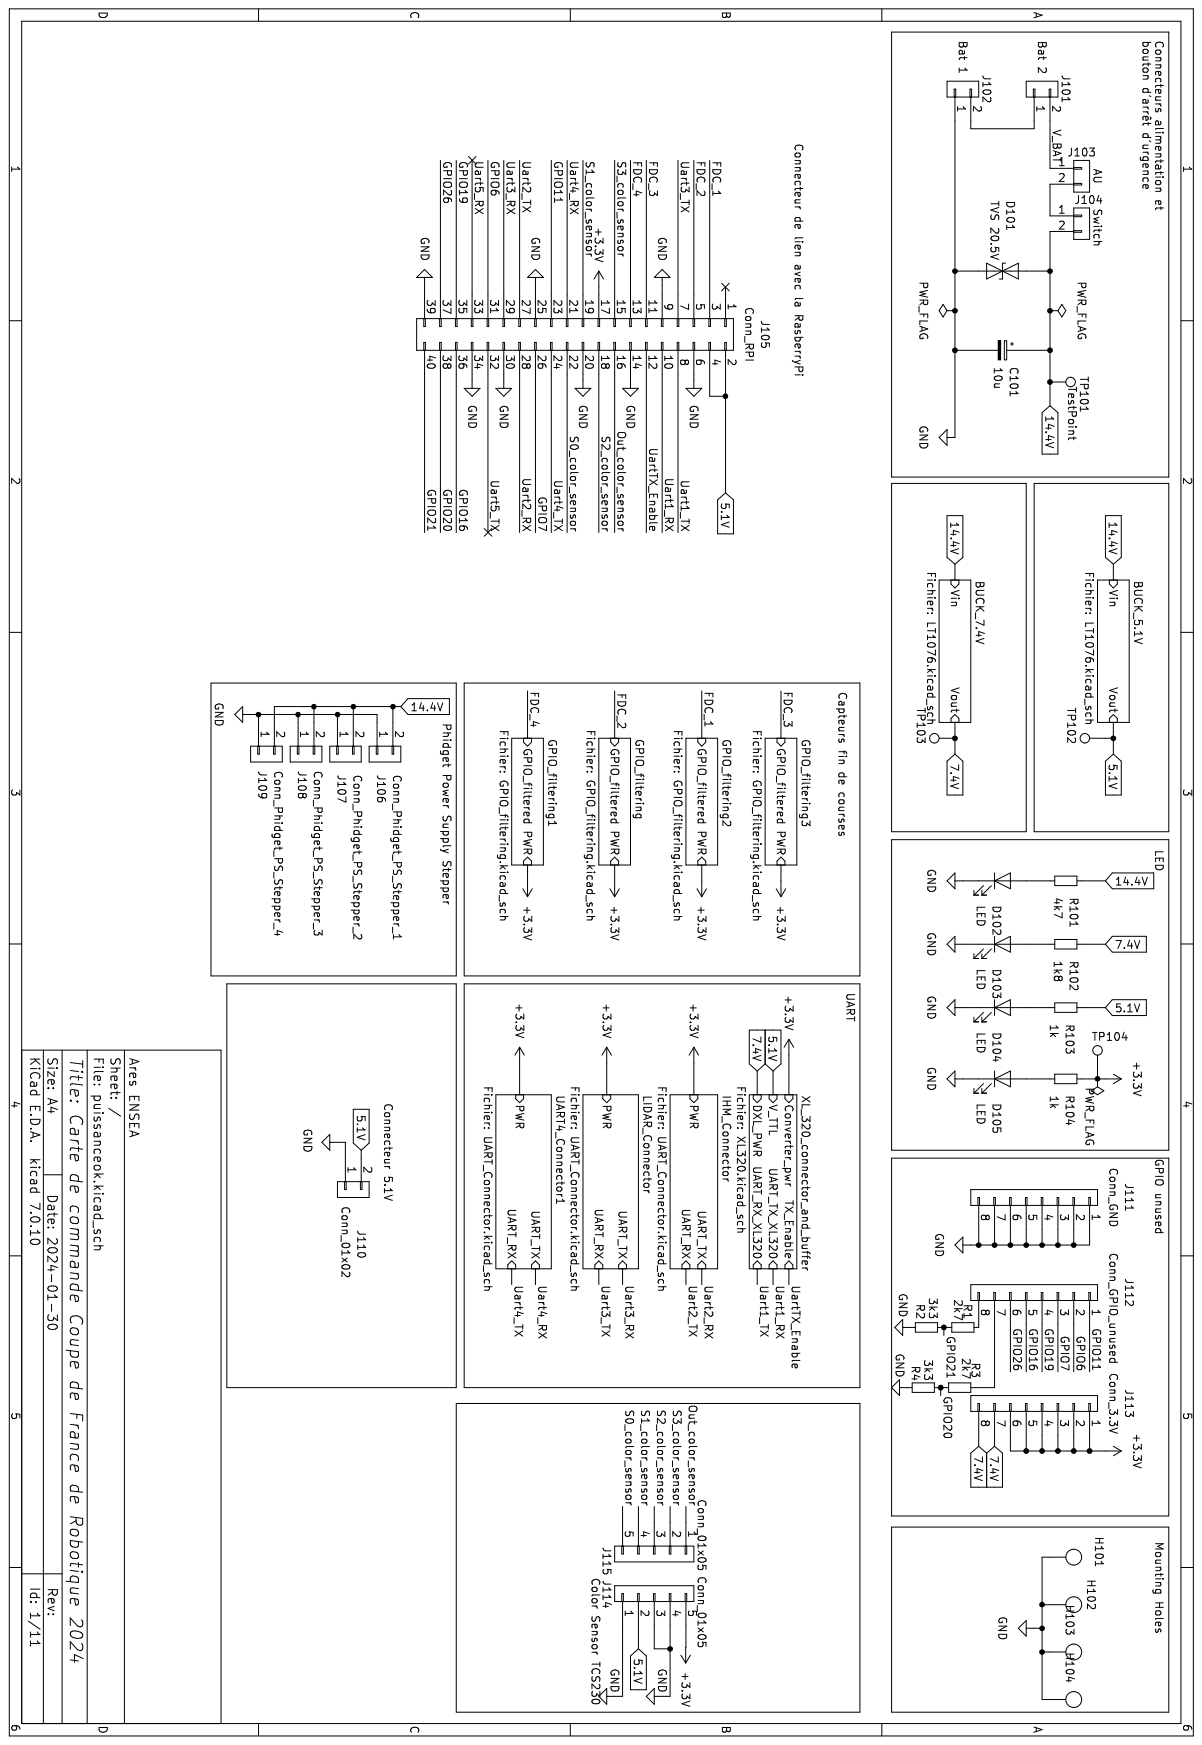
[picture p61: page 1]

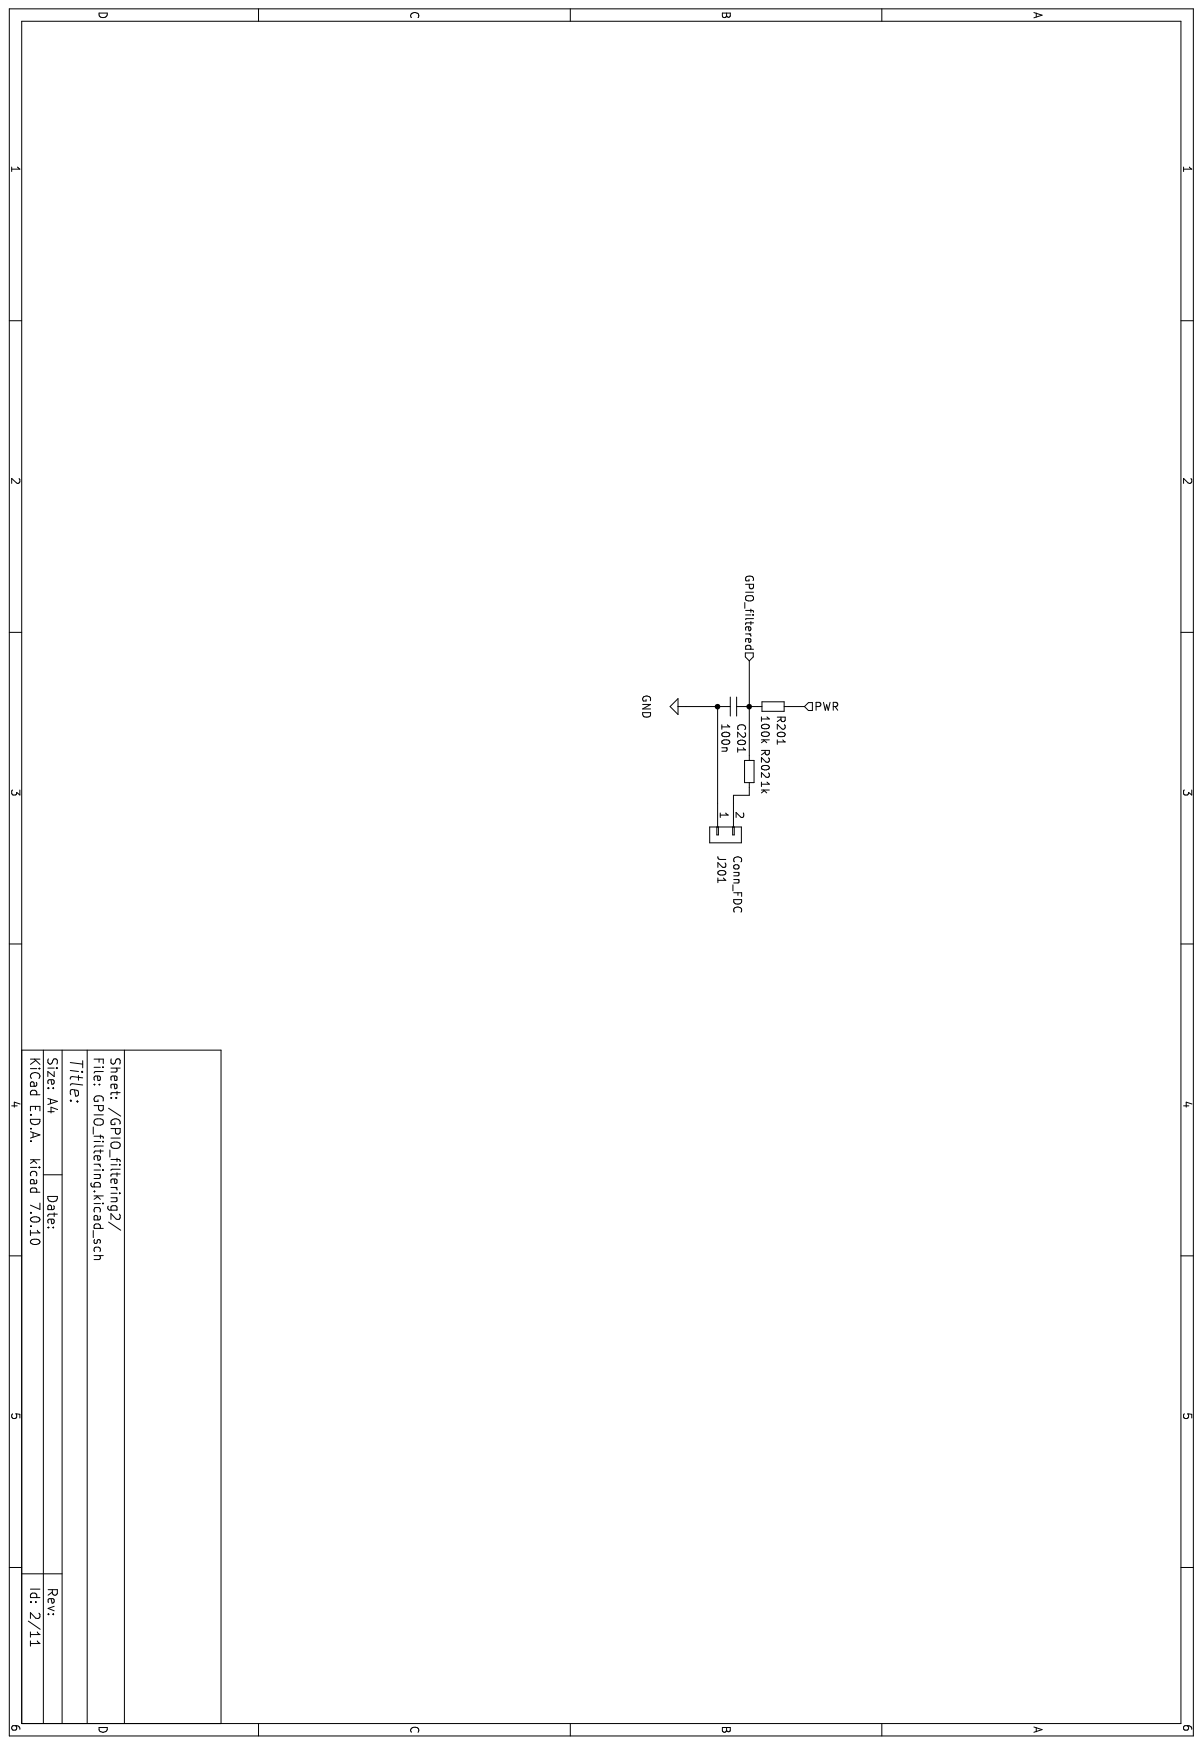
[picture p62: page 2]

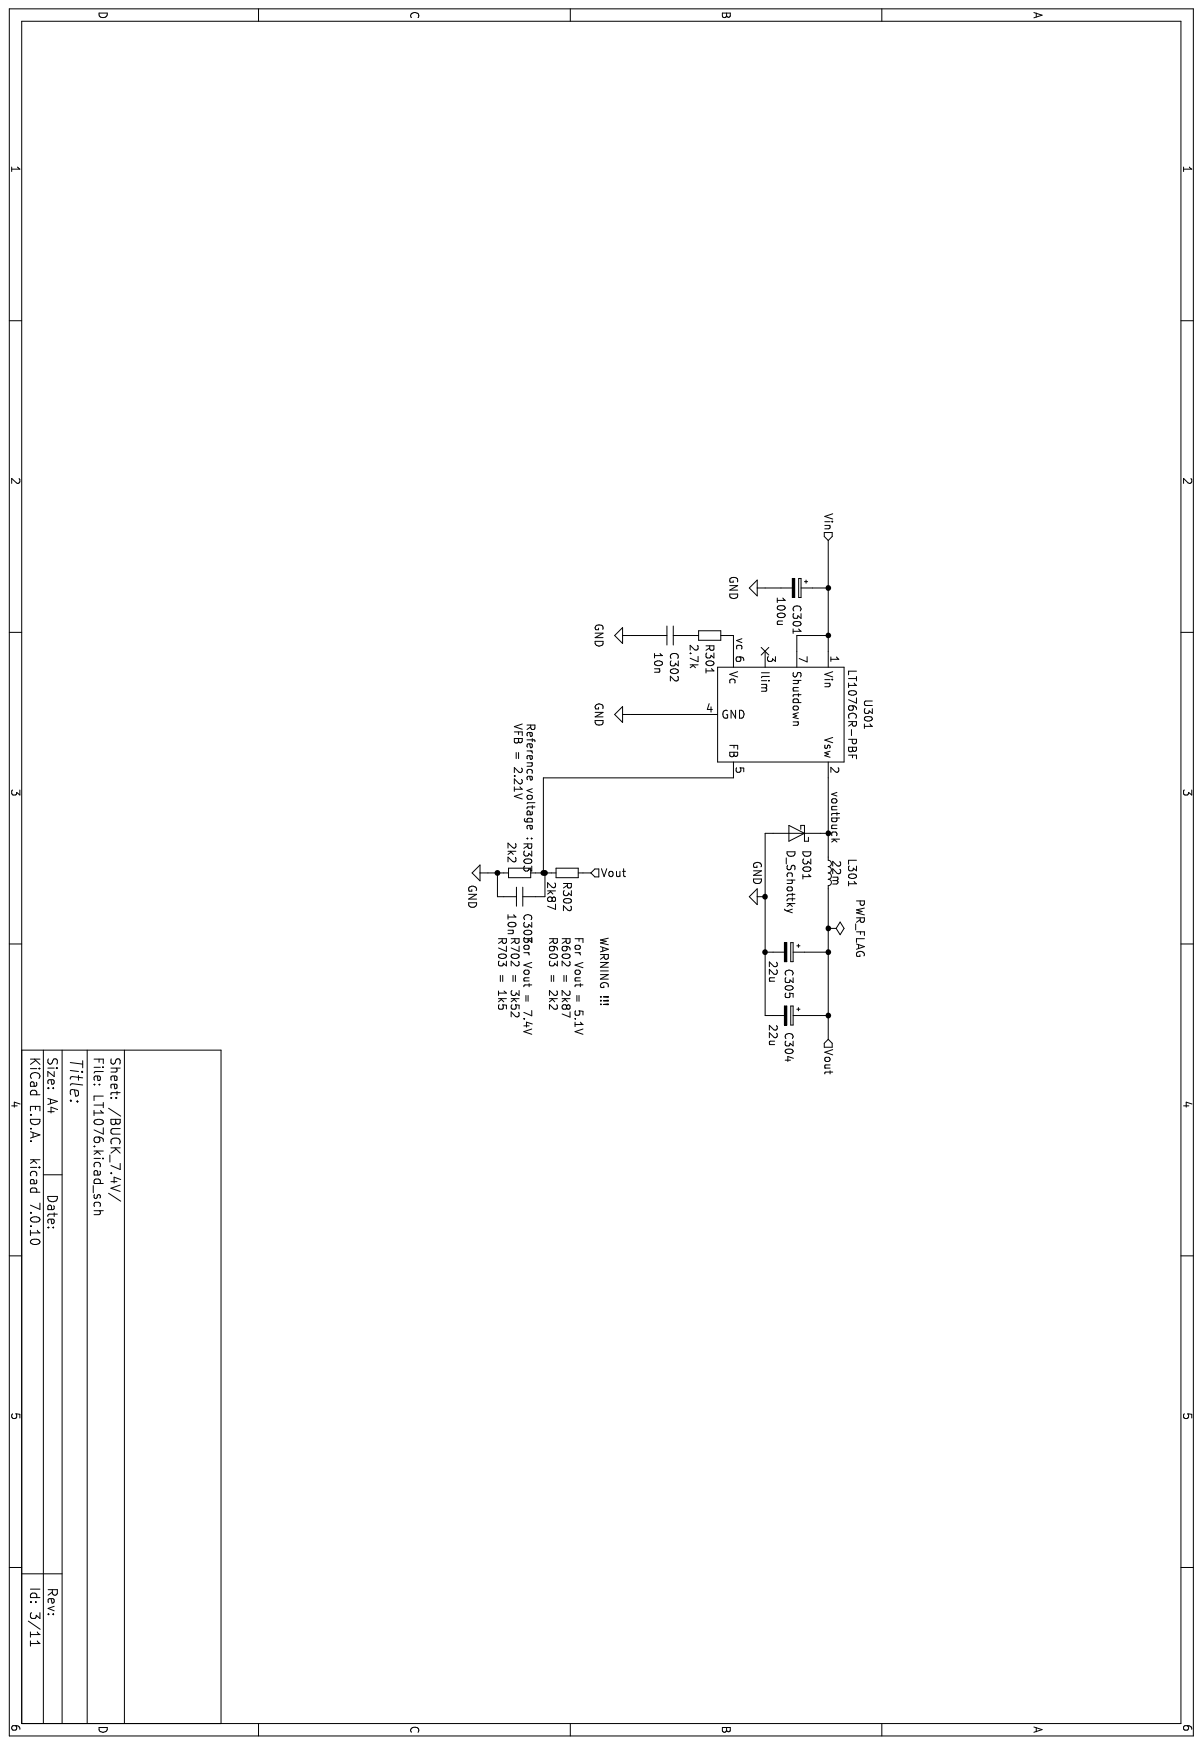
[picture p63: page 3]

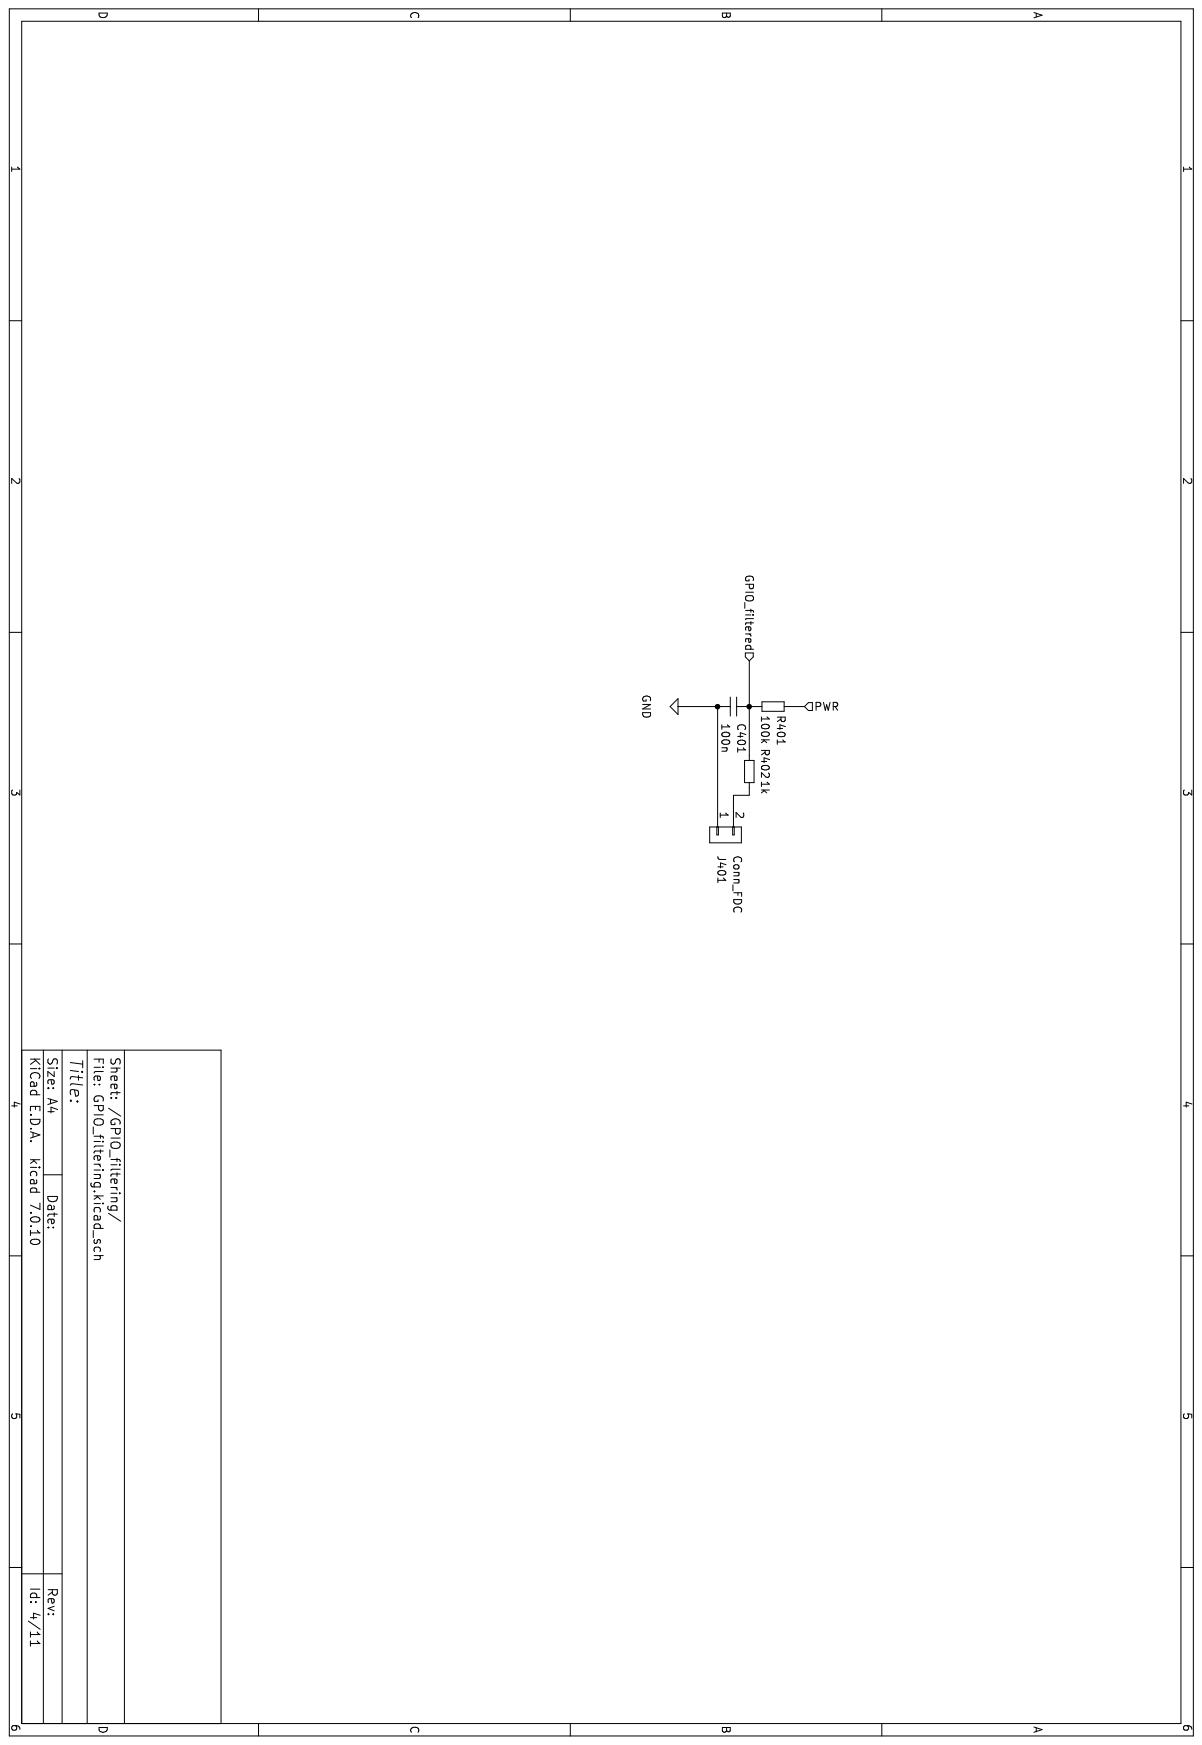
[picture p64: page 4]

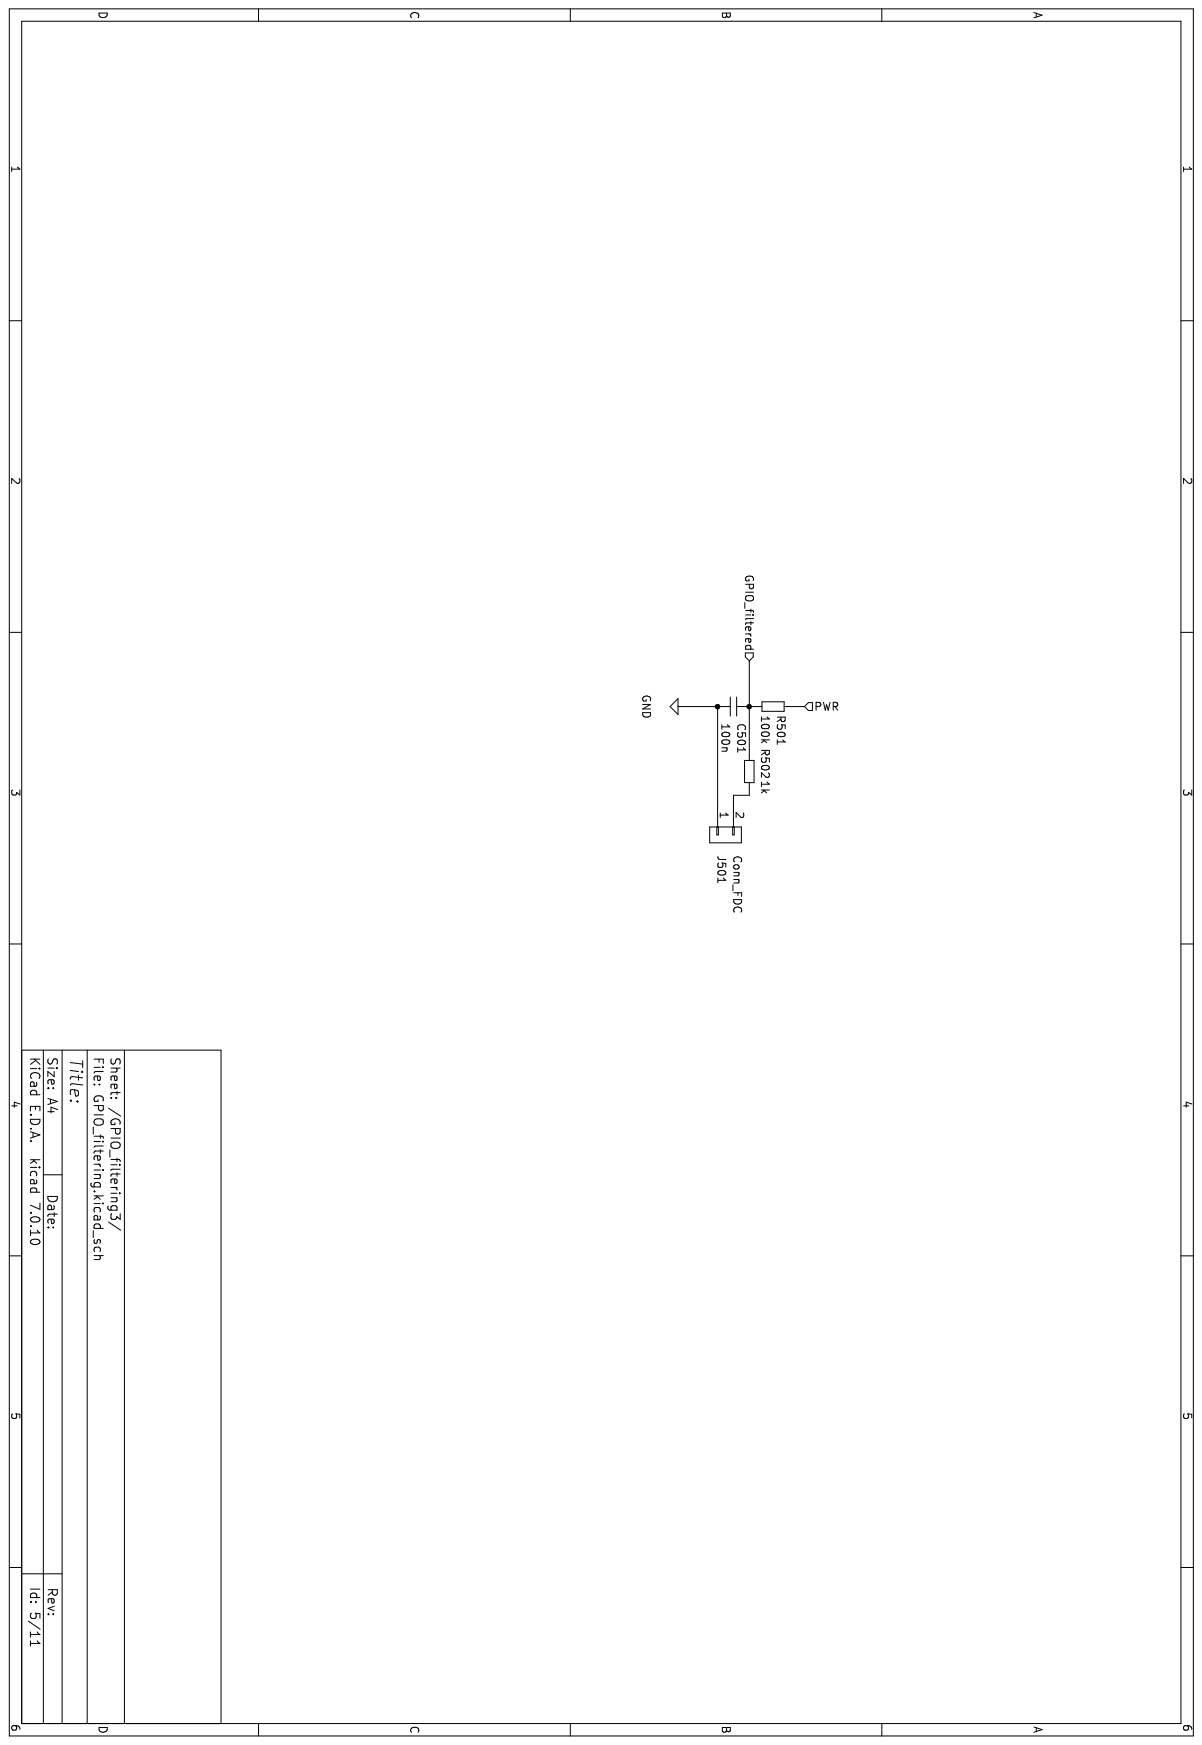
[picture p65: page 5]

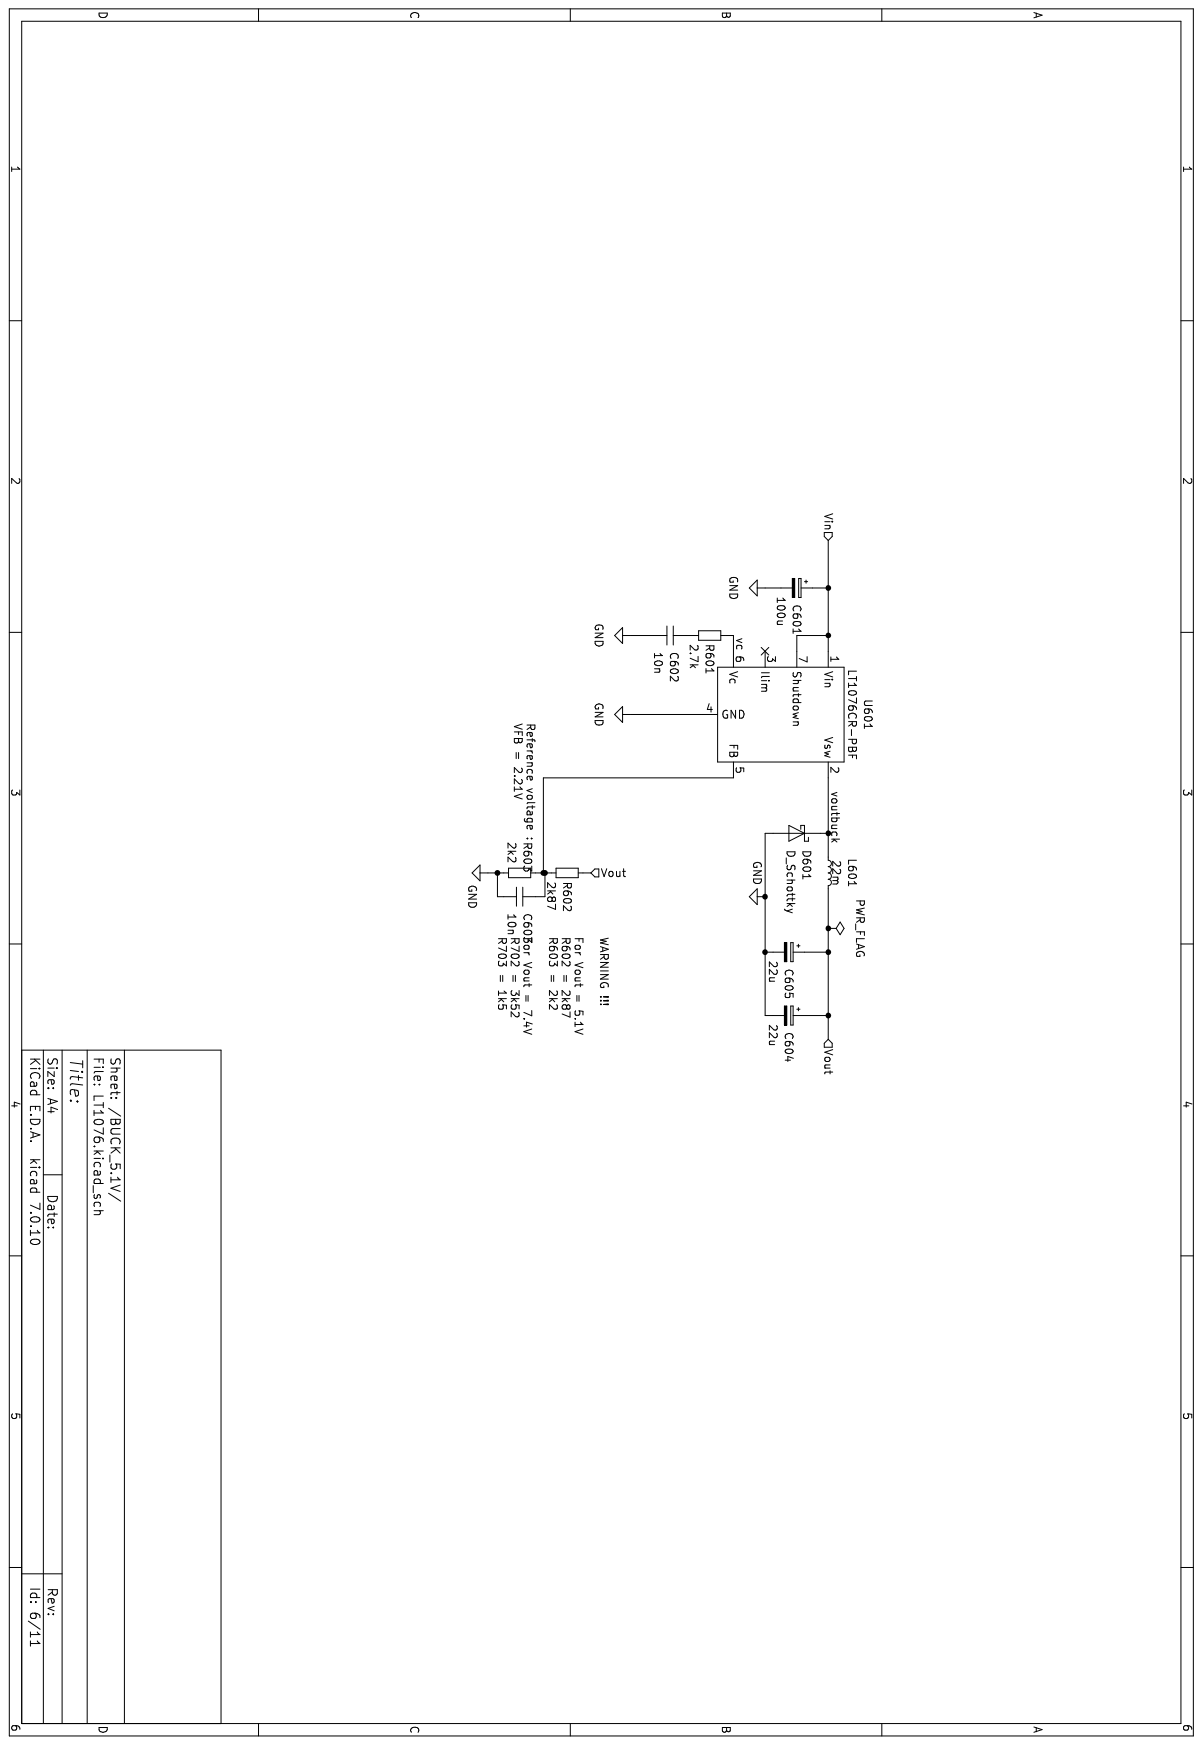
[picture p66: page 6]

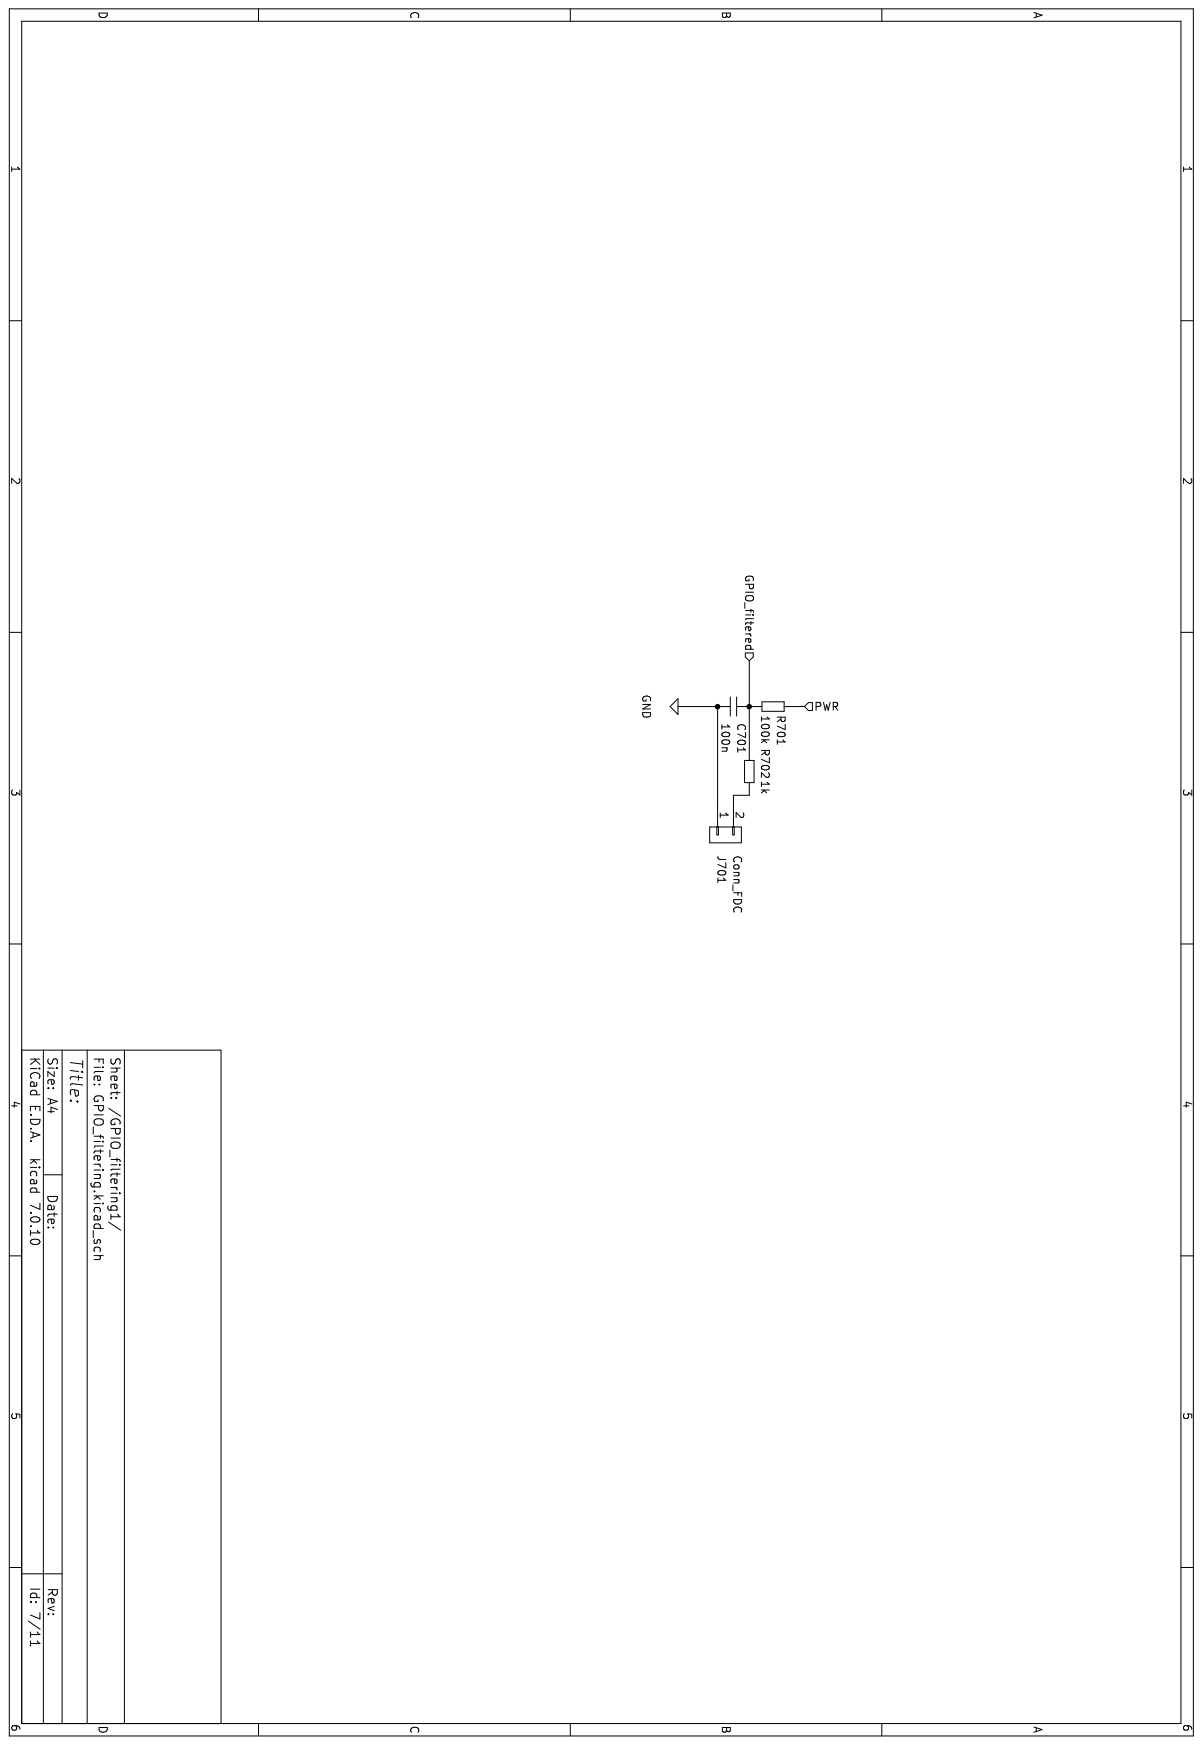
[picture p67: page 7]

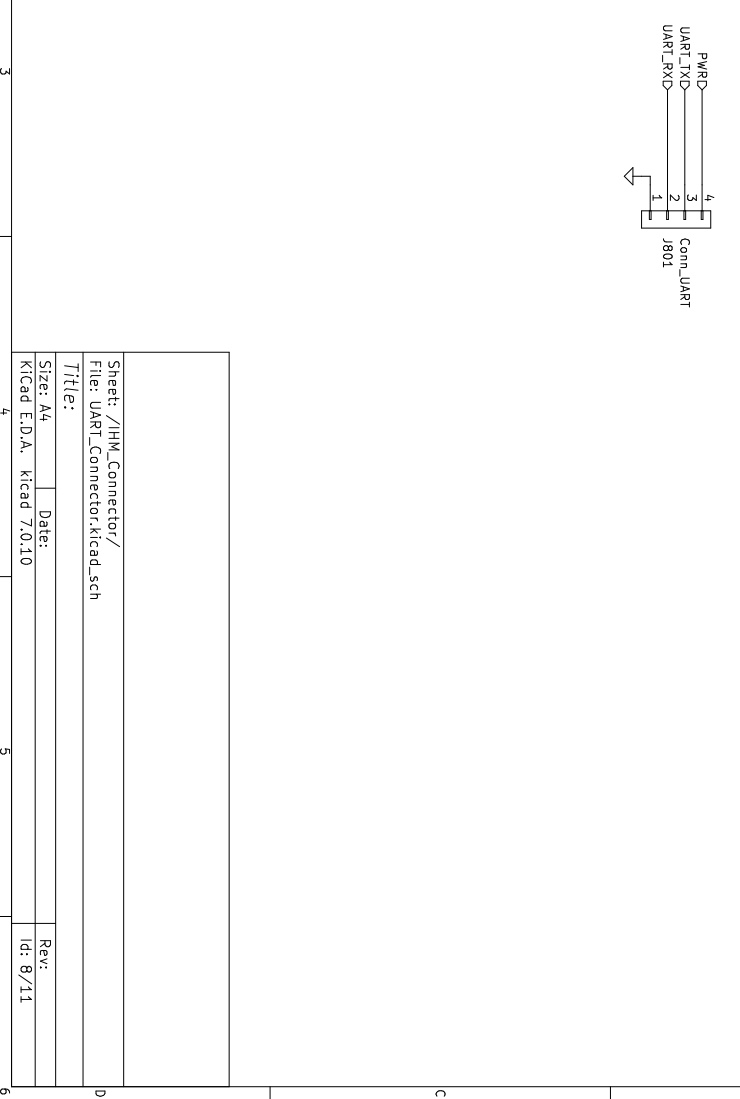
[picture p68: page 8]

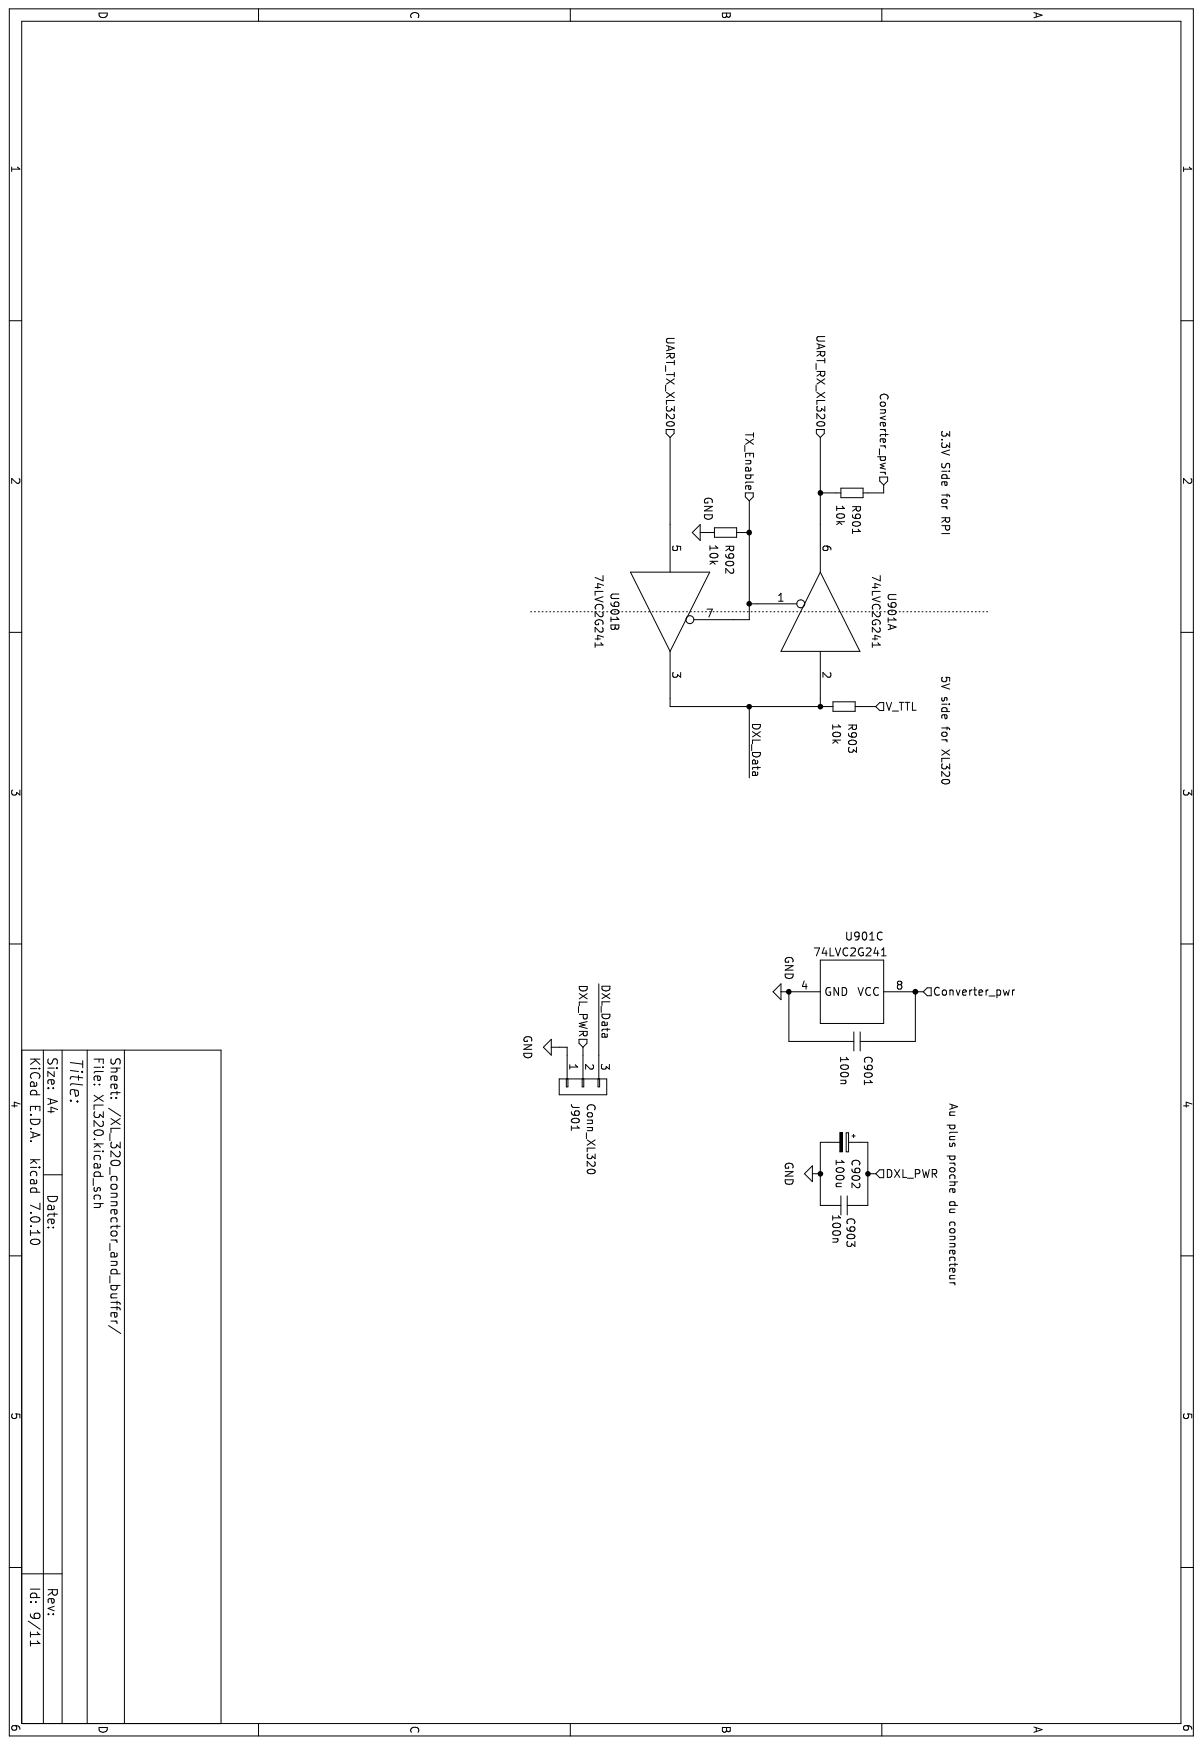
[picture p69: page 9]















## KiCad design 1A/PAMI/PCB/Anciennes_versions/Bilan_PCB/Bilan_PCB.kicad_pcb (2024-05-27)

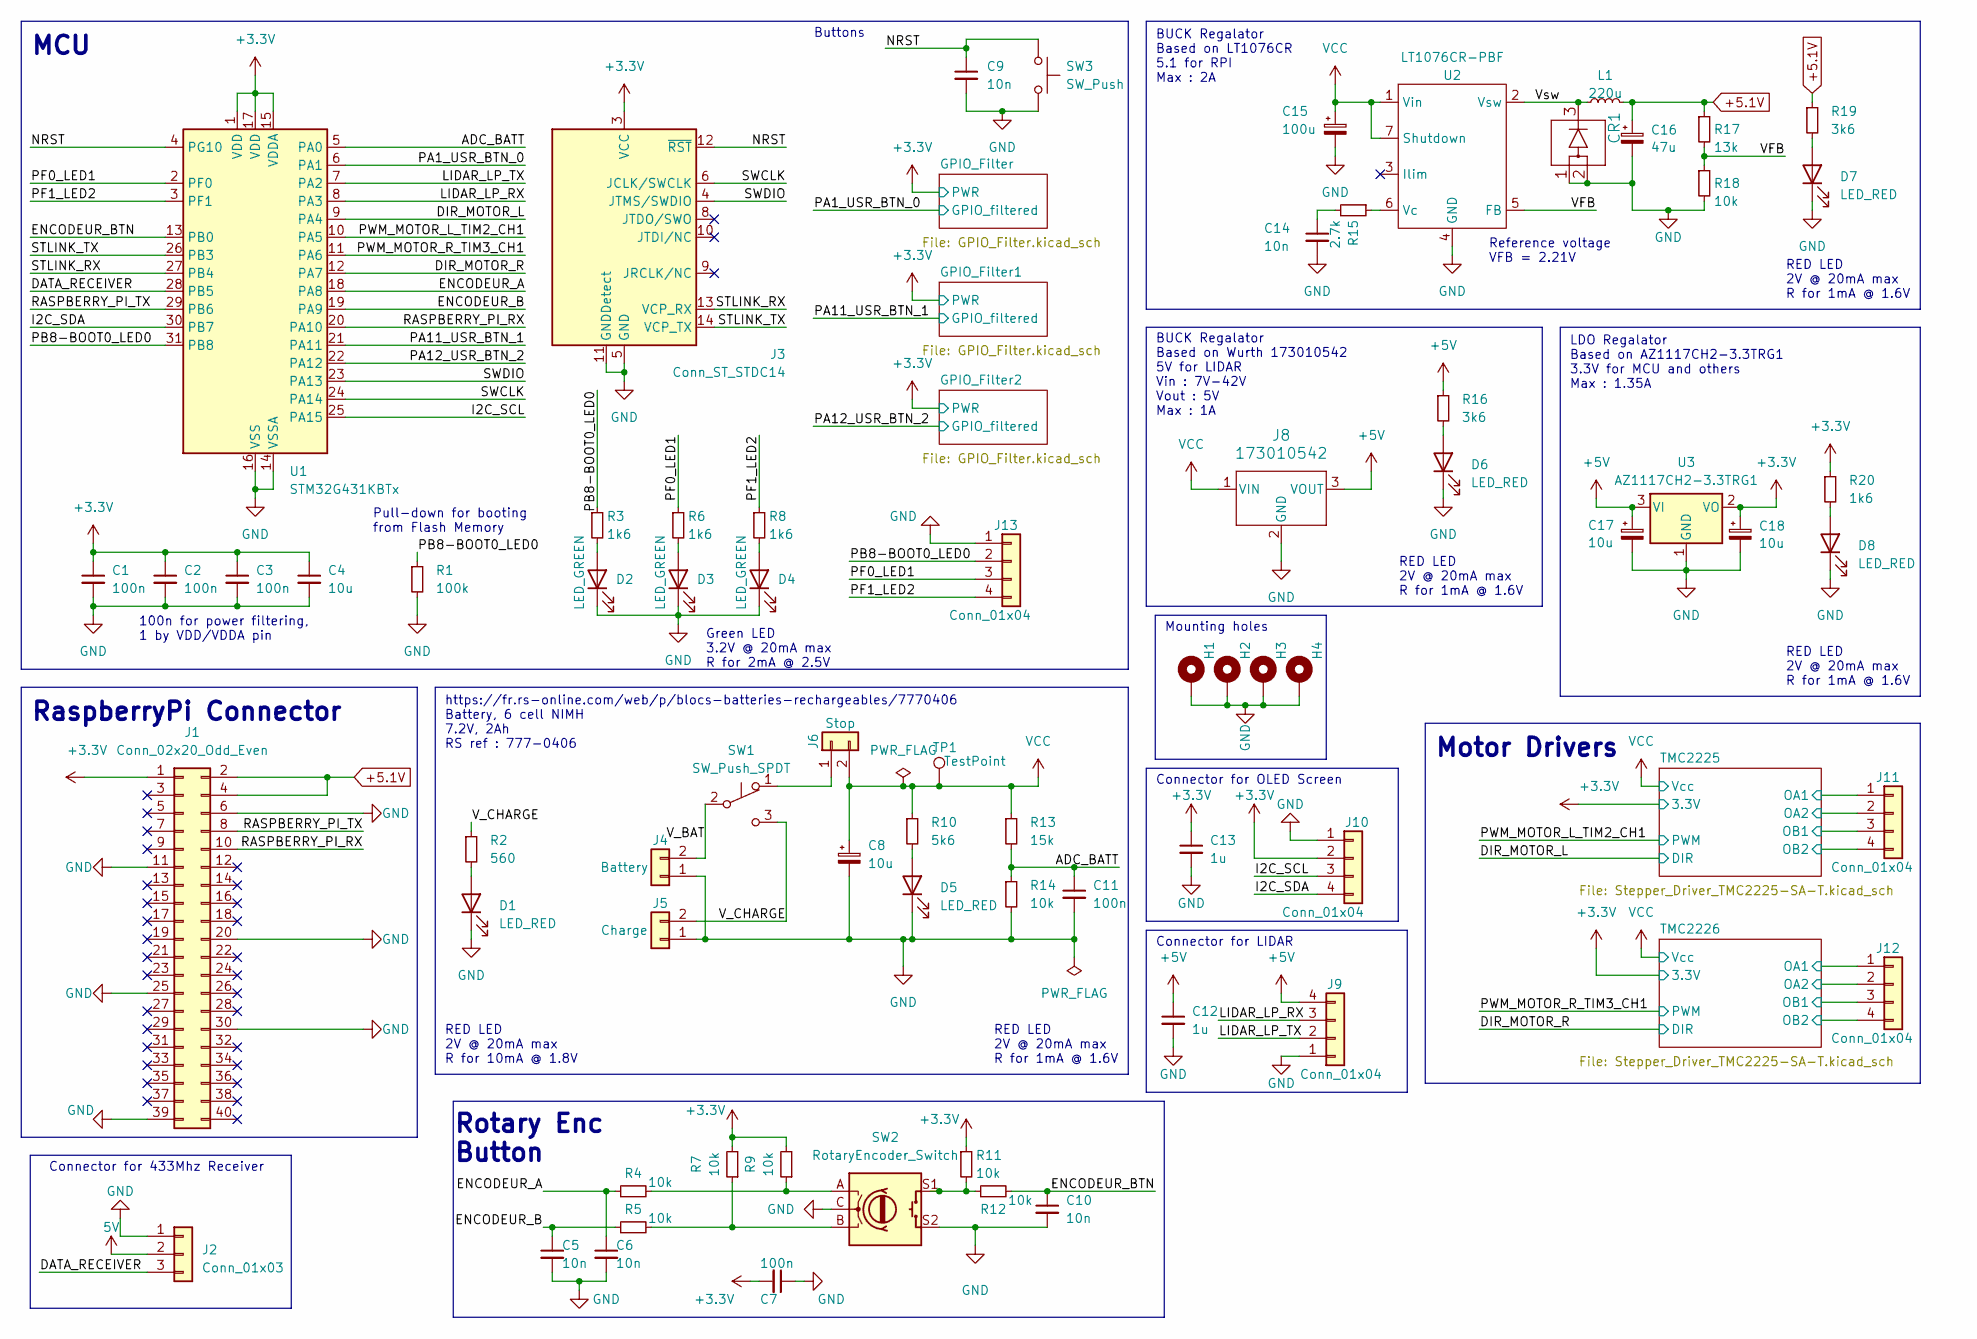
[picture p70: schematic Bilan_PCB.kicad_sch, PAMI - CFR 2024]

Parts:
C1, C2, C3, C7, C11: 100n; C_0402_1005Metric_Pad0.74x0.62mm_HandSolder
C4: 10u; C_0402_1005Metric_Pad0.74x0.62mm_HandSolder
C5, C6, C9, C10, C14: 10n; C_0402_1005Metric_Pad0.74x0.62mm_HandSolder
C8: 10u; CP_Elec_4x5.4; MPN 865060440001
C12, C13: 1u; C_0402_1005Metric_Pad0.74x0.62mm_HandSolder
C15: 100u; CP_Elec_6.3x7.7
C16: 47u; CP_Elec_6.3x5.4
C17, C18: 10u; CP_Elec_6.3x5.4
CR1: DST10100S; DIO_MBR1045STR
D1: LED_RED; LED_0603_1608Metric; MPN 150060RS55040
D2, D3, D4: LED_GREEN; LED_0603_1608Metric_Pad1.05x0.95mm_HandSolder
D5, D6, D7, D8: LED_RED; LED_0603_1608Metric_Pad1.05x0.95mm_HandSolder; MPN 150060RS55040
H1, H2, H3, H4: MountingHole_Pad; MountingHole_2.7mm_M2.5_DIN965_Pad
J1: Conn_02x20_Odd_Even; PinSocket_2x20_P1.00mm_Vertical_SMD
J2: Conn_01x03; JST_XH_B3B-XH-A_1x03_P2.50mm_Vertical
J3: Conn_ST_STDC14; PinHeader_2x07_P1.27mm_Vertical_SMD
J4: Battery; 691322110006; MPN 691322110002
J5: Charge; 691322110006; MPN 691322110002
J6: Stop; 691322110006; MPN 691322110002
J8: 173010542; MPN 173010542
J9, J10, J11, J12, J13: Conn_01x04; JST_XH_B4B-XH-A_1x04_P2.50mm_Vertical
L1: 220u; L_0201_0603Metric
R1: 100k; R_0402_1005Metric_Pad0.72x0.64mm_HandSolder
R2: 560; R_0402_1005Metric_Pad0.72x0.64mm_HandSolder
R3, R6, R8, R20: 1k6; R_0402_1005Metric_Pad0.72x0.64mm_HandSolder
R4, R5, R7, R9, R11, R12, R14, R18: 10k; R_0402_1005Metric_Pad0.72x0.64mm_HandSolder
R10: 5k6; R_0402_1005Metric_Pad0.72x0.64mm_HandSolder
R13: 15k; R_0402_1005Metric_Pad0.72x0.64mm_HandSolder
R15: 2.7k; R_0402_1005Metric_Pad0.72x0.64mm_HandSolder
R16, R19: 3k6; R_0402_1005Metric_Pad0.72x0.64mm_HandSolder
R17: 13k; R_0402_1005Metric_Pad0.72x0.64mm_HandSolder
SW1: SW_Push_SPDT; SW_MINI-SPDT-SW
SW2: RotaryEncoder_Switch; SW_482016514001
SW3: SW_Push; SW_PUSH_6mm
TP1: TestPoint; Pin_D0.9mm_L10.0mm_W2.4mm_FlatFork
U1: STM32G431KBTx; LQFP-32_7x7mm_P0.8mm
U2: LT1076CR-PBF; DPAK127P1394X457-8N
U3: AZ1117CH2-3.3TRG1; SOT230P700X180-4N; MPN AZ1117CH2-3.3TRG1

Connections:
+3.3V: C1.1, C2.1, C3.1, C4.1, C7.2, C13.1, C18.1, J1.1, J2.2, J3.3 (VCC), J10.2, R7.2, R9.2, R11.1, R20.1, U1.1 (VDD), U1.15 (VDDA), U1.17 (VDD), U3.2 (VO); also elsewhere on the board
+5.1V: C16.1, J1.2, J1.4, L1.2, R17.1, R19.1
+5V: C12.1, C17.1, J8.3 (VOUT), J9.4, R16.1, U3.3 (VI)
/ADC_BATT: C11.1, R13.2, R14.1, U1.5 (PA0)
/DATA_RECEIVER: J2.3, U1.28 (PB5)
/DIR_MOTOR_L: U1.9 (PA4); also elsewhere on the board
/DIR_MOTOR_R: U1.12 (PA7); also elsewhere on the board
/ENCODEUR_A: C6.1, R4.1, U1.18 (PA8)
/ENCODEUR_B: C5.1, R5.1, U1.19 (PA9)
/ENCODEUR_BTN: C10.1, R12.2, U1.13 (PB0)
/I2C_SCL: J10.3, U1.25 (PA15)
/I2C_SDA: J10.4, U1.30 (PB7)
/LIDAR_LP_RX: J9.3, U1.8 (PA3)
/LIDAR_LP_TX: J9.2, U1.7 (PA2)
/NRST: C9.1, J3.12 (~RST), SW3.1, U1.4 (PG10)
/PA1_USR_BTN_0: U1.6 (PA1); also elsewhere on the board
/PA11_USR_BTN_1: U1.21 (PA11); also elsewhere on the board
/PA12_USR_BTN_2: U1.22 (PA12); also elsewhere on the board
/PB8-BOOT0_LED0: J13.2, R1.1, R3.1, U1.31 (PB8)
/PF0_LED1: J13.3, R6.1, U1.2 (PF0)
/PF1_LED2: J13.4, R8.1, U1.3 (PF1)
/PWM_MOTOR_L_TIM2_CH1: U1.10 (PA5); also elsewhere on the board
/PWM_MOTOR_R_TIM3_CH1: U1.11 (PA6); also elsewhere on the board
/RASPBERRY_PI_RX: J1.10, U1.20 (PA10)
/RASPBERRY_PI_TX: J1.8, U1.29 (PB6)
/STLINK_RX: J3.13 (VCP_RX), U1.27 (PB4)
/STLINK_TX: J3.14 (VCP_TX), U1.26 (PB3)
/SWCLK: J3.6 (JCLK/SWCLK), U1.24 (PA14)
/SWDIO: J3.4 (JTMS/SWDIO), U1.23 (PA13)
/TMC2225/OA1: J11.1; also elsewhere on the board
/TMC2225/OA2: J11.2; also elsewhere on the board
/TMC2225/OB1: J11.3; also elsewhere on the board
/TMC2225/OB2: J11.4; also elsewhere on the board
/TMC2226/OA1: J12.1; also elsewhere on the board
/TMC2226/OA2: J12.2; also elsewhere on the board
/TMC2226/OB1: J12.3; also elsewhere on the board
/TMC2226/OB2: J12.4; also elsewhere on the board
/VFB: R17.2, R18.1, U2.5 (FB)
/V_BAT: J4.2, SW1.2 (B)
/V_CHARGE: J5.2, R2.1, SW1.3 (C)
/Vsw: CR1.3, L1.1, U2.2 (Vsw)
GND: C1.2, C2.2, C3.2, C4.2, C5.2, C6.2, C7.1, C8.2, C9.2, C10.2, C11.2, C12.2, C13.2, C14.2, C15.2, C16.2, C17.2, C18.2, CR1.1, CR1.2, D1.1 (K), D2.1 (K), D3.1 (K), D4.1 (K), D5.1 (K), D6.1 (K), D7.1 (K), D8.1 (K), H1.1, H2.1, H3.1, H4.1, J1.6, J1.11, J1.20, J1.25, J1.30, J1.39, J2.1, J3.5 (GND), J3.7 (GND), J3.11 (GNDDetect), J4.1, J5.1, J8.2 (GND), J9.1, J10.1, J13.1, R1.2, R14.2, R18.2, SW2.C, SW2.S2, SW3.2, U1.14 (VSSA), U1.16 (VSS), U1.32 (VSS), U2.4 (GND), U3.1 (GND); also elsewhere on the board
unnamed: C14.1, R15.2
unnamed: D1.2 (A), R2.2
unnamed: D2.2 (A), R3.2
unnamed: D3.2 (A), R6.2
unnamed: D4.2 (A), R8.2
unnamed: D5.2 (A), R10.2
unnamed: D6.2 (A), R16.2
unnamed: D7.2 (A), R19.2
unnamed: D8.2 (A), R20.2
unnamed: J6.1, SW1.1 (A)
unnamed: R4.2, R9.1, SW2.A
unnamed: R5.2, R7.1, SW2.B
unnamed: R11.2, R12.1, SW2.S1
unnamed: R15.1, U2.6 (Vc)
VCC: C8.1, C15.1, J6.2, J8.1 (VIN), R10.1, R13.1, TP1.1, U2.1 (Vin), U2.7 (Shutdown); also elsewhere on the board

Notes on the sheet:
Rotary Enc Button
BUCK Regalator Based on Wurth 173010542 5V for LIDAR Vin : 7V-42V Vout : 5V Max : 1A
RED LED 2V @ 20mA max R for 1mA @ 1.6V
MCU
Motor Drivers
Mounting holes
LDO Regalator Based on AZ1117CH2-3.3TRG1 3.3V for MCU and others Max : 1.35A
RaspberryPi Connector
100n for power filtering, 1 by VDD/VDDA pin
Reference voltage VFB = 2.21V
Green LED 3.2V @ 20mA max R for 2mA @ 2.5V
Connector for 433Mhz Receiver
Buttons
BUCK Regalator Based on LT1076CR 5.1 for RPI Max : 2A
RED LED 2V @ 20mA max R for 10mA @ 1.8V
Connector for LIDAR
Connector for OLED Screen
Pull-down for booting from Flash Memory
https://fr.rs-online.com/web/p/blocs-batteries-rechargeables/7770406 Battery, 6 cell NIMH 7.2V, 2Ah RS ref : 777-0406

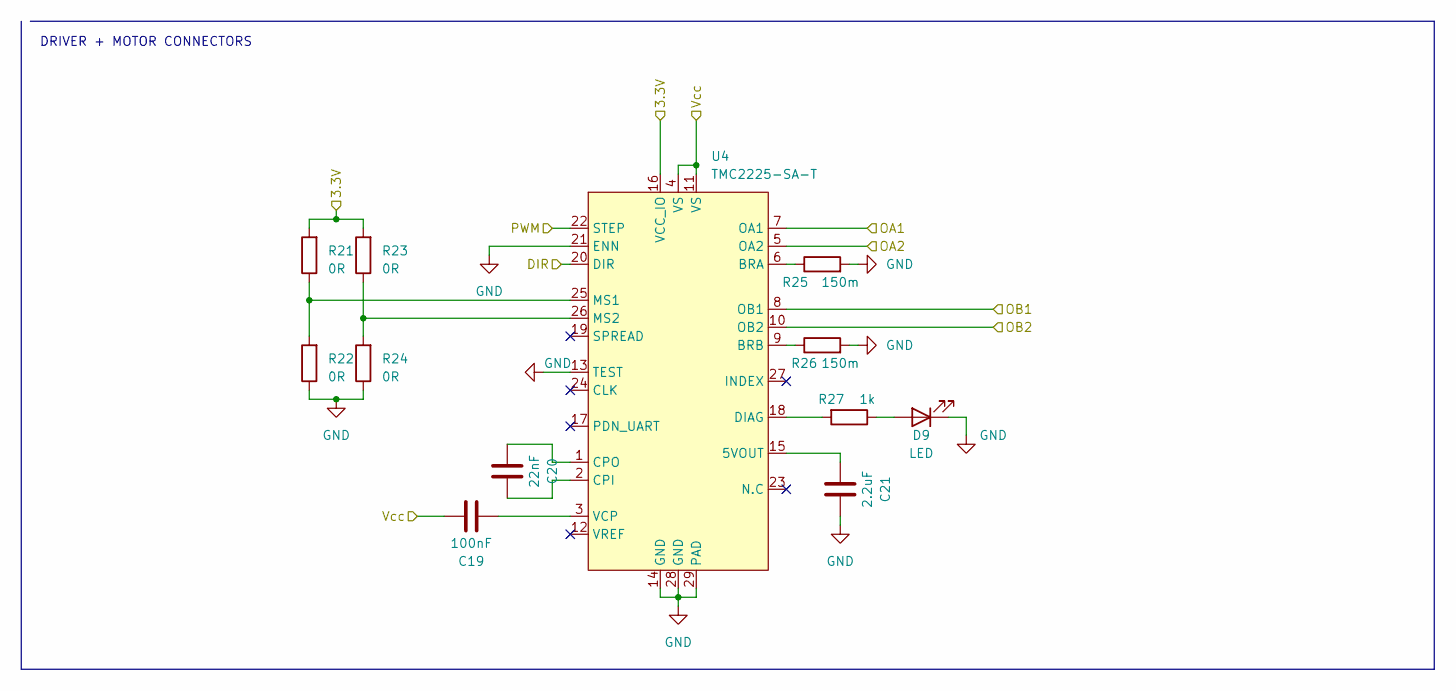
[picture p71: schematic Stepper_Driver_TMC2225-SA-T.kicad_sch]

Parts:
C19: 100nF; C_0603_1608Metric_Pad1.08x0.95mm_HandSolder
C20: 22nF; C_0603_1608Metric_Pad1.08x0.95mm_HandSolder
C21: 2.2uF; C_0805_2012Metric_Pad1.18x1.45mm_HandSolder
D9: LED; LED_0603_1608Metric_Pad1.05x0.95mm_HandSolder
R21, R22, R23, R24: 0R; R_0603_1608Metric_Pad0.98x0.95mm_HandSolder
R25, R26: 150m; R_1206_3216Metric_Pad1.30x1.75mm_HandSolder
R27: 1k; R_0603_1608Metric_Pad0.98x0.95mm_HandSolder
U4: TMC2225-SA-T; HTSSOP-28-1EP_4.4x9.7mm_P0.65mm_EP2.85x5.4mm_ThermalVias

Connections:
+3.3V: R21.2, R23.2, U4.16 (VCC_IO); also elsewhere on the board
/DIR_MOTOR_L: U4.20 (DIR); also elsewhere on the board
/PWM_MOTOR_L_TIM2_CH1: U4.22 (STEP); also elsewhere on the board
/TMC2225/OA1: U4.7 (OA1); also elsewhere on the board
/TMC2225/OA2: U4.5 (OA2); also elsewhere on the board
/TMC2225/OB1: U4.8 (OB1); also elsewhere on the board
/TMC2225/OB2: U4.10 (OB2); also elsewhere on the board
GND: C21.1, D9.1 (K), R22.1, R24.1, R25.2, R26.2, U4.13 (TEST), U4.14 (GND), U4.21 (ENN), U4.28 (GND), U4.29 (PAD); also elsewhere on the board
unnamed: D9.2 (A), R27.1
unnamed: C21.2, U4.15 (5VOUT)
unnamed: R25.1, U4.6 (BRA)
unnamed: R26.1, U4.9 (BRB)
unnamed: C20.1, U4.2 (CPI)
unnamed: C20.2, U4.1 (CPO)
unnamed: R27.2, U4.18 (DIAG)
unnamed: R21.1, R22.2, U4.25 (MS1)
unnamed: R23.1, R24.2, U4.26 (MS2)
unnamed: C19.2, U4.3 (VCP)
VCC: C19.1, U4.4 (VS), U4.11 (VS); also elsewhere on the board

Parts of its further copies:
C22: 100nF; C_0603_1608Metric_Pad1.08x0.95mm_HandSolder
C23: 22nF; C_0603_1608Metric_Pad1.08x0.95mm_HandSolder
C24: 2.2uF; C_0805_2012Metric_Pad1.18x1.45mm_HandSolder
D10: LED; LED_0603_1608Metric_Pad1.05x0.95mm_HandSolder
R28, R29, R30, R31: 0R; R_0603_1608Metric_Pad0.98x0.95mm_HandSolder
R32, R33: 150m; R_1206_3216Metric_Pad1.30x1.75mm_HandSolder
R34: 1k; R_0603_1608Metric_Pad0.98x0.95mm_HandSolder
U5: TMC2225-SA-T; HTSSOP-28-1EP_4.4x9.7mm_P0.65mm_EP2.85x5.4mm_ThermalVias

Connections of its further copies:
+3.3V: R28.2, R30.2, U5.16 (VCC_IO); also elsewhere on the board
/DIR_MOTOR_R: U5.20 (DIR); also elsewhere on the board
/PWM_MOTOR_R_TIM3_CH1: U5.22 (STEP); also elsewhere on the board
/TMC2226/OA1: U5.7 (OA1); also elsewhere on the board
/TMC2226/OA2: U5.5 (OA2); also elsewhere on the board
/TMC2226/OB1: U5.8 (OB1); also elsewhere on the board
/TMC2226/OB2: U5.10 (OB2); also elsewhere on the board
GND: C24.1, D10.1 (K), R29.1, R31.1, R32.2, R33.2, U5.13 (TEST), U5.14 (GND), U5.21 (ENN), U5.28 (GND), U5.29 (PAD); also elsewhere on the board
unnamed: D10.2 (A), R34.1
unnamed: C24.2, U5.15 (5VOUT)
unnamed: R32.1, U5.6 (BRA)
unnamed: R33.1, U5.9 (BRB)
unnamed: C23.1, U5.2 (CPI)
unnamed: C23.2, U5.1 (CPO)
unnamed: R34.2, U5.18 (DIAG)
unnamed: R28.1, R29.2, U5.25 (MS1)
unnamed: R30.1, R31.2, U5.26 (MS2)
unnamed: C22.2, U5.3 (VCP)
VCC: C22.1, U5.4 (VS), U5.11 (VS); also elsewhere on the board

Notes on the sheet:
DRIVER + MOTOR CONNECTORS

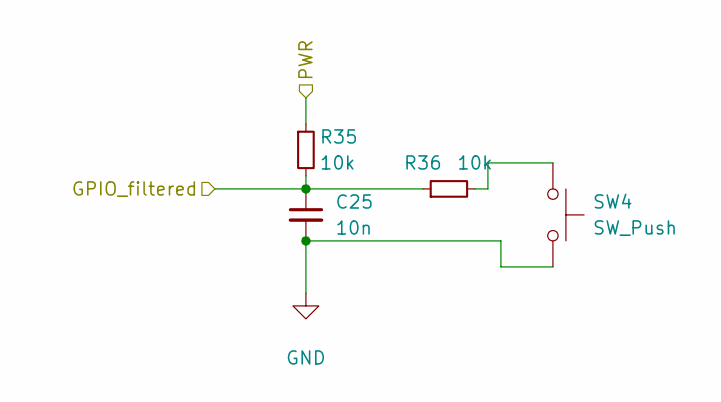
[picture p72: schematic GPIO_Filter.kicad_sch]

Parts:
C25: 10n; C_0402_1005Metric_Pad0.74x0.62mm_HandSolder
R35, R36: 10k; R_0402_1005Metric_Pad0.72x0.64mm_HandSolder
SW4: SW_Push; SW_PUSH_6mm

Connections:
+3.3V: R35.1; also elsewhere on the board
/PA1_USR_BTN_0: C25.1, R35.2, R36.1; also elsewhere on the board
GND: C25.2, SW4.2; also elsewhere on the board
unnamed: R36.2, SW4.1

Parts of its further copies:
C26, C27: 10n; C_0402_1005Metric_Pad0.74x0.62mm_HandSolder
R37, R38, R39, R40: 10k; R_0402_1005Metric_Pad0.72x0.64mm_HandSolder
SW5, SW6: SW_Push; SW_PUSH_6mm

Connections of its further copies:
+3.3V: R37.1, R39.1; also elsewhere on the board
/PA11_USR_BTN_1: C26.1, R37.2, R38.1; also elsewhere on the board
/PA12_USR_BTN_2: C27.1, R39.2, R40.1; also elsewhere on the board
GND: C26.2, C27.2, SW5.2, SW6.2; also elsewhere on the board
unnamed: R38.2, SW5.1
unnamed: R40.2, SW6.1

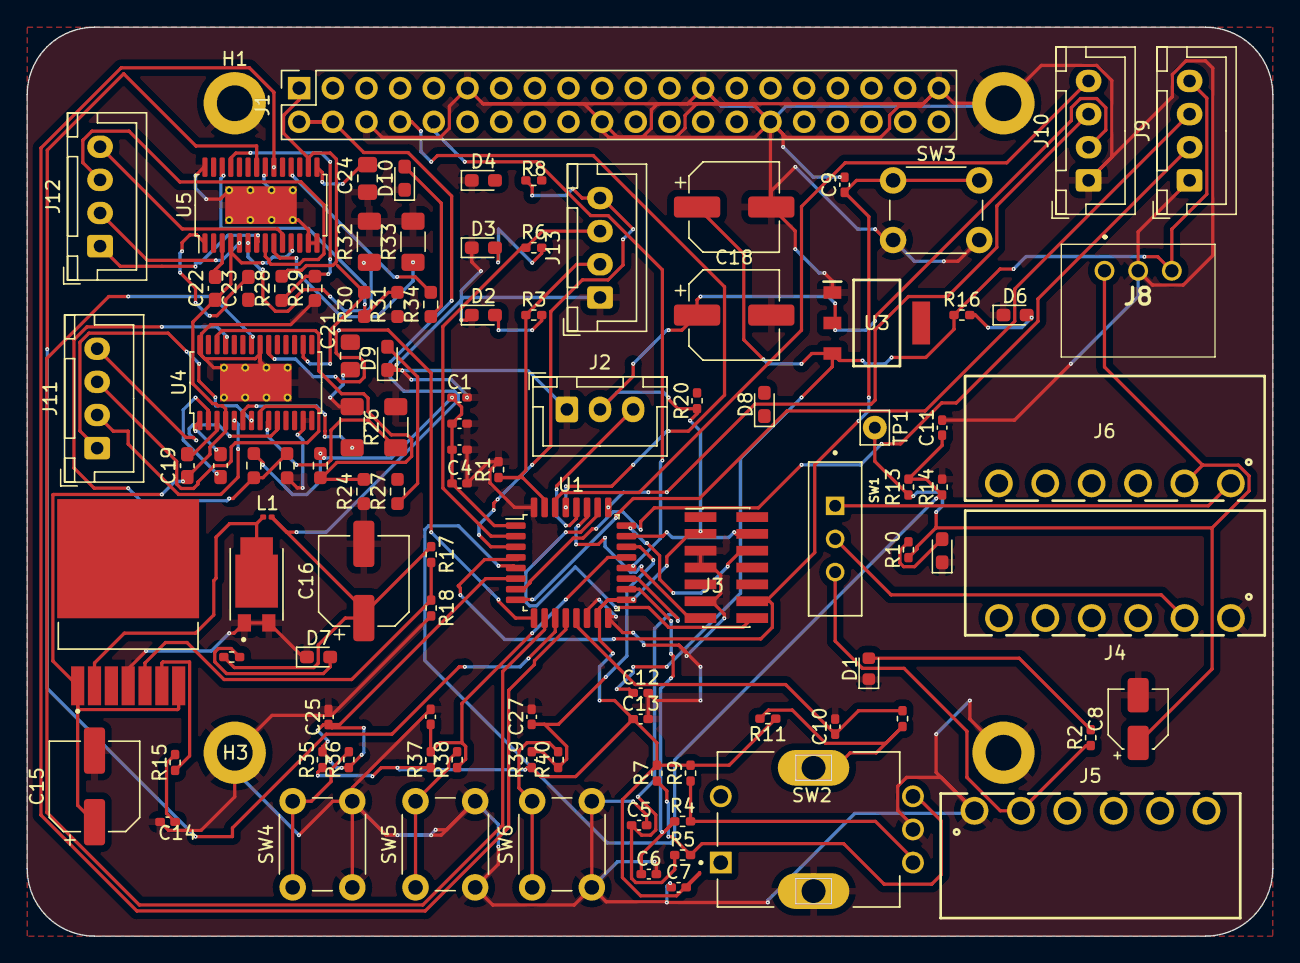
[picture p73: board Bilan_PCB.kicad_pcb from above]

Board: 2 copper layers, 94.0 x 68.6 mm, 107 parts (0 on the bottom side), 80 nets.

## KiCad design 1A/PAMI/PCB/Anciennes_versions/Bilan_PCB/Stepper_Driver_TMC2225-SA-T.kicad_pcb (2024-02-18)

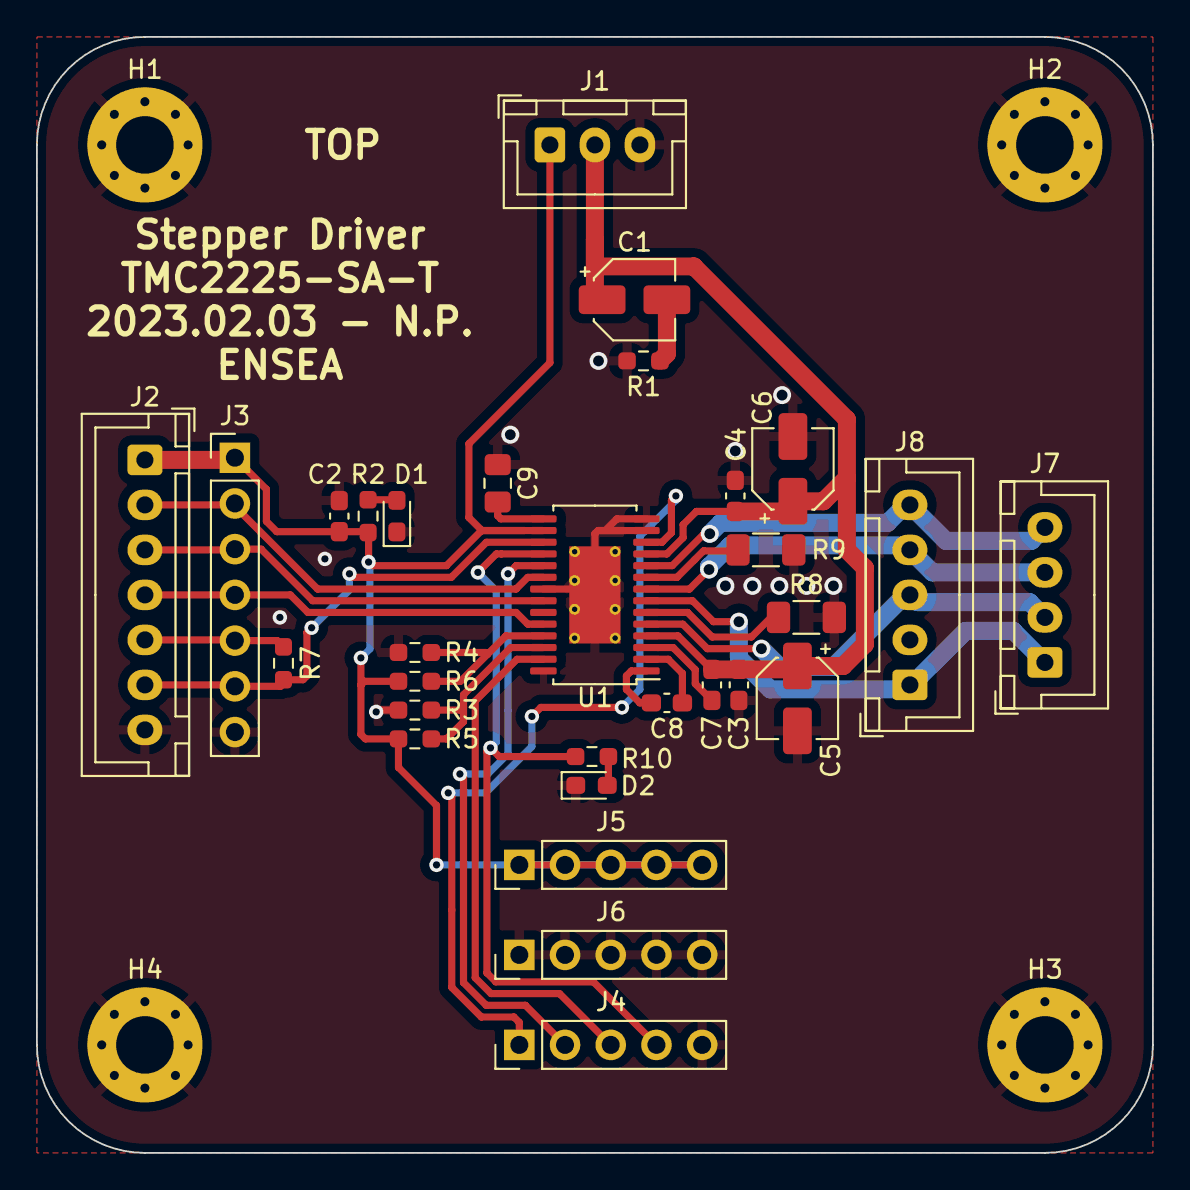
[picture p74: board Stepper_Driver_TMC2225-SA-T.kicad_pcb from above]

Board: 2 copper layers, 62.0 x 62.0 mm, 34 parts (0 on the bottom side), 27 nets.

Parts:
C1, C5, C6: 10uF; CP_Elec_4x5.7
C2, C3, C4, C7: 100nF; C_0603_1608Metric_Pad1.08x0.95mm_HandSolder
C8: 22nF; C_0603_1608Metric_Pad1.08x0.95mm_HandSolder
C9: 2.2uF; C_0805_2012Metric_Pad1.18x1.45mm_HandSolder
D1, D2: LED; LED_0603_1608Metric_Pad1.05x0.95mm_HandSolder
H1, H2, H3, H4: MountingHole_Pad; MountingHole_3.2mm_M3_Pad_Via
J1: Conn_01x03_Male; JST_XH_B3B-XH-A_1x03_P2.50mm_Vertical
J2: Conn_01x07; JST_XH_B7B-XH-A_1x07_P2.50mm_Vertical
J3: Conn_01x07; PinHeader_1x07_P2.54mm_Vertical
J4, J5, J6: Conn_01x05; PinHeader_1x05_P2.54mm_Vertical
J7: Conn_01x04_Female; JST_XH_B4B-XH-A_1x04_P2.50mm_Vertical
J8: Conn_01x05_Female; JST_XH_B5B-XH-A_1x05_P2.50mm_Vertical
R1: 110m; R_0603_1608Metric_Pad0.98x0.95mm_HandSolder
R2, R7, R10: 1k; R_0603_1608Metric_Pad0.98x0.95mm_HandSolder
R3, R4, R5, R6: 0R; R_0603_1608Metric_Pad0.98x0.95mm_HandSolder
R8, R9: 150m; R_1206_3216Metric_Pad1.30x1.75mm_HandSolder
U1: TMC2225-SA-T; HTSSOP-28-1EP_4.4x9.7mm_P0.65mm_EP2.85x5.4mm_ThermalVias

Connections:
5VOUT: C9.2, U1.15 (5VOUT)
+3.3V: C2.1, J1.1, J2.1, J3.1, J5.1, J5.2, J5.3, J5.4, J5.5, R2.1, R3.2, R5.2, U1.16 (VCC_IO)
BRA: R8.1, U1.6 (BRA)
BRB: R9.1, U1.9 (BRB)
CLK: J2.4, J3.4, U1.24 (CLK)
DIAG: J4.4, R10.2, U1.18 (DIAG)
DIR: J2.2, J3.2, U1.20 (DIR)
GND: C2.2, C3.2, C4.2, C5.2, C6.2, C9.1, D1.1 (K), D2.1 (K), H1.1, H2.1, H3.1, H4.1, J1.3, J2.7, J3.7, J4.5, J6.1, J6.2, J6.3, J6.4, J6.5, R1.2, R4.1, R6.1, R8.2, R9.2, U1.13 (TEST), U1.14 (GND), U1.21 (ENN), U1.28 (GND), U1.29 (PAD)
INDEX: J4.3, U1.27 (INDEX)
MS1: R3.1, R4.2, U1.25 (MS1)
MS2: R5.1, R6.2, U1.26 (MS2)
unnamed: C1.2, R1.1
unnamed: C8.1, U1.2 (CPI)
unnamed: C8.2, U1.1 (CPO)
unnamed: D1.2 (A), R2.2
unnamed: D2.2 (A), R10.1
OA1: J7.1, J8.1, U1.7 (OA1)
OA2: J7.2, J8.3, U1.5 (OA2)
OB1: J7.3, J8.4, U1.8 (OB1)
OB2: J7.4, J8.5, U1.10 (OB2)
SPREAD: J4.2, U1.19 (SPREAD)
STEP: J2.3, J3.3, U1.22 (STEP)
UART_RX: J2.6, J3.6, R7.1, U1.17 (PDN_UART)
UART_TX: J2.5, J3.5, R7.2
VCC: C1.1, C3.1, C4.1, C5.1, C6.1, C7.1, J1.2, U1.4 (VS), U1.11 (VS)
VCP: C7.2, U1.3 (VCP)
VREF: J4.1, U1.12 (VREF)

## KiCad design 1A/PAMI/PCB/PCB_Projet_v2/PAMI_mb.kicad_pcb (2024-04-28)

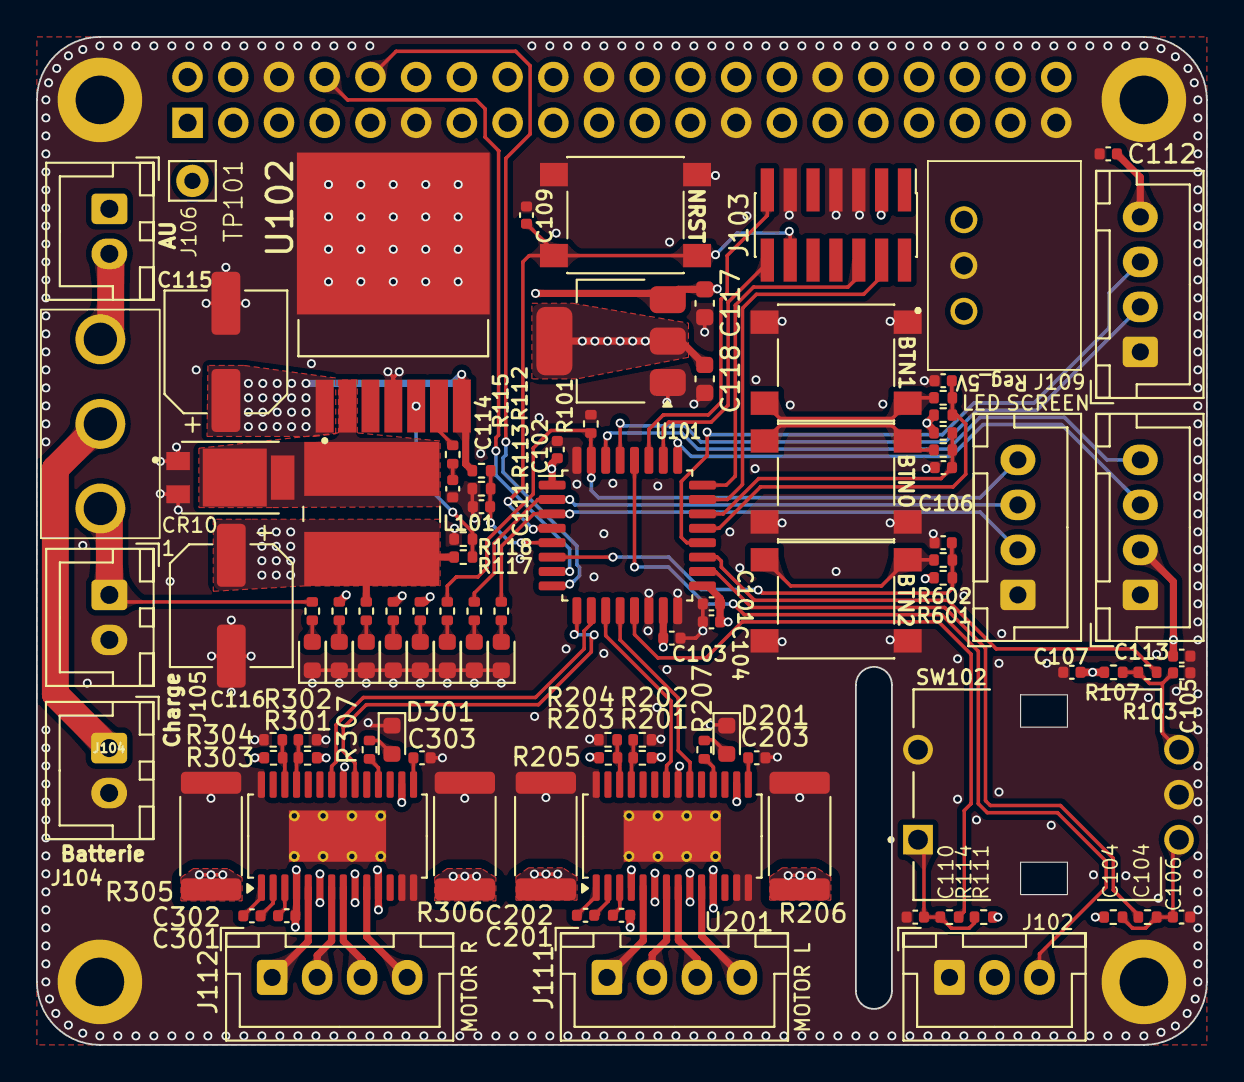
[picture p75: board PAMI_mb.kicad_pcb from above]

Board: 4 copper layers, 65.0 x 56.0 mm, 106 parts (1 on the bottom side), 80 nets.

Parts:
C101, C102, C103, C107, C111, C201, C301: 100n; C_0402_1005Metric
C104: 10u; C_0402_1005Metric
C105, C106, C109, C110, C114, C401, C501, C601: 10n; C_0402_1005Metric
C112, C113: 1u; C_0402_1005Metric
C115: 100u; CP_Elec_6.3x7.7
C116: 47u; CP_Elec_6.3x5.4
C117, C118: 10u; C_0603_1608Metric
C202, C302: 22n; C_0402_1005Metric
C203, C303: 2u2; C_0402_1005Metric
CR101: DST10100S; DIO_MBR1045STR
D101, D105, D106, D107, D108: LED_RED; LED_0603_1608Metric
D102, D103, D104: LED_GREEN; LED_0603_1608Metric
D201, D301: LED; LED_0603_1608Metric
H101, H102, H103, H104: MountingHole_Pad; MountingHole_2.7mm_M2.5_DIN965_Pad
J101: Conn_02x20_Odd_Even; PinSocket_2x20_P2.54mm_Vertical
J102: Conn_01x03; JST_XH_B3B-XH-A_1x03_P2.50mm_Vertical
J103: Conn_ST_STDC14; PinHeader_2x07_P1.27mm_Vertical_SMD
J104: Battery; JST_XH_B2B-XH-A_1x02_P2.50mm_Vertical
J105: Charge; JST_XH_B2B-XH-A_1x02_P2.50mm_Vertical
J106: Stop; JST_XH_B2B-XH-A_1x02_P2.50mm_Vertical
J107, J109, J110, J111, J112: Conn_01x04; JST_XH_B4B-XH-A_1x04_P2.50mm_Vertical
J108: 173010542
L101: 220u; L_Wuerth_WE-PD2-Typ-L
R101: 100k; R_0402_1005Metric
R102: 560; R_0402_1005Metric
R103, R105, R107, R109, R111, R113, R114, R118, R401, R402, R501, R502, R601, R602: 10k; R_0402_1005Metric
R104, R106, R108, R120: 1k6; R_0402_1005Metric
R110: 5k6; R_0402_1005Metric
R112: 15k; R_0402_1005Metric
R115: 2.7k; R_0402_1005Metric
R116, R119: 3k6; R_0402_1005Metric
R117: 13k; R_0402_1005Metric
R201, R202, R203, R204, R301, R302, R303, R304: 0R; R_0402_1005Metric
R205, R206, R305, R306: 150m; R_2512_6332Metric
R207, R307: 1k; R_0402_1005Metric
SW101: SW_Push_SPDT; 472121010111
SW102: RotaryEncoder_Switch; SW_482016514001
SW103, SW401, SW501, SW601: SW_Push; SW_Push_1P1T_NO_6x6mm_H9.5mm
TP101: TestPoint; Pin_D0.9mm_L10.0mm_W2.4mm_FlatFork
U101: STM32G431KBTx; LQFP-32_7x7mm_P0.8mm
U102: LT1076CR-PBF; DPAK127P1394X457-8N
U103: AZ1117CH2-3.3TRG1; SOT-223-3_TabPin2
U201, U301: TMC2225-SA-T; HTSSOP-28-1EP_4.4x9.7mm_P0.65mm_EP2.85x5.4mm_ThermalVias

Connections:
+3.3V: C101.1, C102.1, C103.1, C104.1, C107.2, C113.1, C118.1, J102.2, J103.3 (VCC), J110.2, R107.2, R109.2, R111.1, R120.1, R201.2, R203.2, R301.2, R303.2, R401.1, R501.1, R601.1, U101.1 (VDD), U101.15 (VDDA), U101.17 (VDD), U103.2 (VO), U201.16 (VCC_IO), U301.16 (VCC_IO)
+5.1V: C116.1, J101.2, J101.4, L101.2, R117.1, R119.1
+5V: C112.1, C117.1, J108.3 (VOUT), J109.4, R116.1, U103.3 (VI)
/ADC_BATT: C111.1, R112.2, R113.1, U101.5 (PA0)
/DATA_RECEIVER: J102.3, U101.28 (PB5)
/DIR_MOTOR_L: U101.12 (PA7), U201.20 (DIR)
/DIR_MOTOR_R: U101.9 (PA4), U301.20 (DIR)
/ENCODEUR_A: R105.1, U101.18 (PA8)
/ENCODEUR_B: R103.1, U101.19 (PA9)
/ENCODEUR_BTN: R114.2, U101.13 (PB0)
/I2C_SCL: J110.3, U101.25 (PA15)
/I2C_SDA: J110.4, U101.30 (PB7)
/LIDAR_LP_RX: J109.3, U101.20 (PA10)
/LIDAR_LP_TX: J109.2, U101.29 (PB6)
/NRST: C109.1, J103.12 (~RST), SW103.1, U101.4 (PG10)
/PA1_USR_BTN_0: C401.1, R401.2, R402.1, U101.22 (PA12)
/PA11_USR_BTN_1: C501.1, R501.2, R502.1, U101.21 (PA11)
/PA12_USR_BTN_2: C601.1, R601.2, R602.1, U101.6 (PA1)
/PB8-BOOT0_LED0: J107.4, R101.1, R104.1, U101.31 (PB8)
/PF0_LED1: J107.3, R106.1, U101.2 (PF0)
/PF1_LED2: J107.2, R108.1, U101.3 (PF1)
/PWM_MOTOR_L_TIM2_CH1: U101.11 (PA6), U201.22 (STEP)
/PWM_MOTOR_R_TIM3_CH1: U101.10 (PA5), U301.22 (STEP)
/RASPBERRY_PI_RX: J101.10, U101.8 (PA3)
/RASPBERRY_PI_TX: J101.8, U101.7 (PA2)
/STLINK_RX: J103.13 (VCP_RX), U101.27 (PB4)
/STLINK_TX: J103.14 (VCP_TX), U101.26 (PB3)
/SWCLK: J103.6 (JCLK/SWCLK), U101.24 (PA14)
/SWDIO: J103.4 (JTMS/SWDIO), U101.23 (PA13)
/TMC2225/OA1: J111.2, U201.7 (OA1)
/TMC2225/OA2: J111.1, U201.5 (OA2)
/TMC2225/OB1: J111.3, U201.8 (OB1)
/TMC2225/OB2: J111.4, U201.10 (OB2)
/TMC2226/OA1: J112.2, U301.7 (OA1)
/TMC2226/OA2: J112.1, U301.5 (OA2)
/TMC2226/OB1: J112.3, U301.8 (OB1)
/TMC2226/OB2: J112.4, U301.10 (OB2)
/VFB: R117.2, R118.1, U102.5 (FB)
/V_BAT: J104.1, SW101.2 (B)
/V_CHARGE: J105.1, R102.1, SW101.3 (C)
/Vsw: CR101.3, L101.1, U102.2 (Vsw)
GND: C101.2, C102.2, C103.2, C104.2, C105.2, C106.2, C107.1, C109.2, C110.2, C111.2, C112.2, C113.2, C114.2, C115.2, C116.2, C117.2, C118.2, C203.1, C303.1, C401.2, C501.2, C601.2, CR101.1, CR101.2, D101.1 (K), D102.1 (K), D103.1 (K), D104.1 (K), D105.1 (K), D106.1 (K), D107.1 (K), D108.1 (K), D201.1 (K), D301.1 (K), H101.1, H102.1, H103.1, H104.1, J101.6, J101.11, J101.20, J101.25, J101.30, J101.39, J102.1, J103.5 (GND), J103.7 (GND), J103.11 (GNDDetect), J104.2, J105.2, J107.1, J108.2 (GND), J109.1, J110.1, R101.2, R113.2, R118.2, R202.1, R204.1, R205.2, R206.2, R302.1, R304.1, R305.2, R306.2, SW102.C, SW102.S2, SW103.2, SW401.2, SW501.2, SW601.2, U101.14 (VSSA), U101.16 (VSS), U101.32 (VSS), U102.4 (GND), U103.1 (GND), U201.13 (TEST), U201.14 (GND), U201.21 (ENN), U201.28 (GND), U201.29 (PAD), U301.13 (TEST), U301.14 (GND), U301.21 (ENN), U301.28 (GND), U301.29 (PAD)
unnamed: C105.1, R103.2, R107.1, SW102.B
unnamed: C106.1, R105.2, R109.1, SW102.A
unnamed: C110.1, R111.2, R114.1, SW102.S1
unnamed: C114.1, R115.2
unnamed: D101.2 (A), R102.2
unnamed: D102.2 (A), R104.2
unnamed: D103.2 (A), R106.2
unnamed: D104.2 (A), R108.2
unnamed: D105.2 (A), R110.2
unnamed: D106.2 (A), R116.2
unnamed: D107.2 (A), R119.2
unnamed: D108.2 (A), R120.2
unnamed: D201.2 (A), R207.1
unnamed: D301.2 (A), R307.1
unnamed: J106.2, SW101.1 (A)
unnamed: R402.2, SW401.1
unnamed: R502.2, SW501.1
unnamed: R602.2, SW601.1
unnamed: R115.1, U102.6 (Vc)
unnamed: C203.2, U201.15 (5VOUT)
unnamed: R205.1, U201.6 (BRA)
unnamed: R206.1, U201.9 (BRB)
unnamed: C202.1, U201.2 (CPI)
unnamed: C202.2, U201.1 (CPO)
unnamed: R207.2, U201.18 (DIAG)
unnamed: R201.1, R202.2, U201.25 (MS1)
unnamed: R203.1, R204.2, U201.26 (MS2)
unnamed: C201.2, U201.3 (VCP)
unnamed: C303.2, U301.15 (5VOUT)
unnamed: R305.1, U301.6 (BRA)
unnamed: R306.1, U301.9 (BRB)
unnamed: C302.1, U301.2 (CPI)
unnamed: C302.2, U301.1 (CPO)
unnamed: R307.2, U301.18 (DIAG)
unnamed: R301.1, R302.2, U301.25 (MS1)
unnamed: R303.1, R304.2, U301.26 (MS2)
unnamed: C301.2, U301.3 (VCP)
VCC: C115.1, C201.1, C301.1, J106.1, J108.1 (VIN), R110.1, R112.1, TP101.1, U102.1 (Vin), U102.7 (Shutdown), U201.4 (VS), U201.11 (VS), U301.4 (VS), U301.11 (VS)

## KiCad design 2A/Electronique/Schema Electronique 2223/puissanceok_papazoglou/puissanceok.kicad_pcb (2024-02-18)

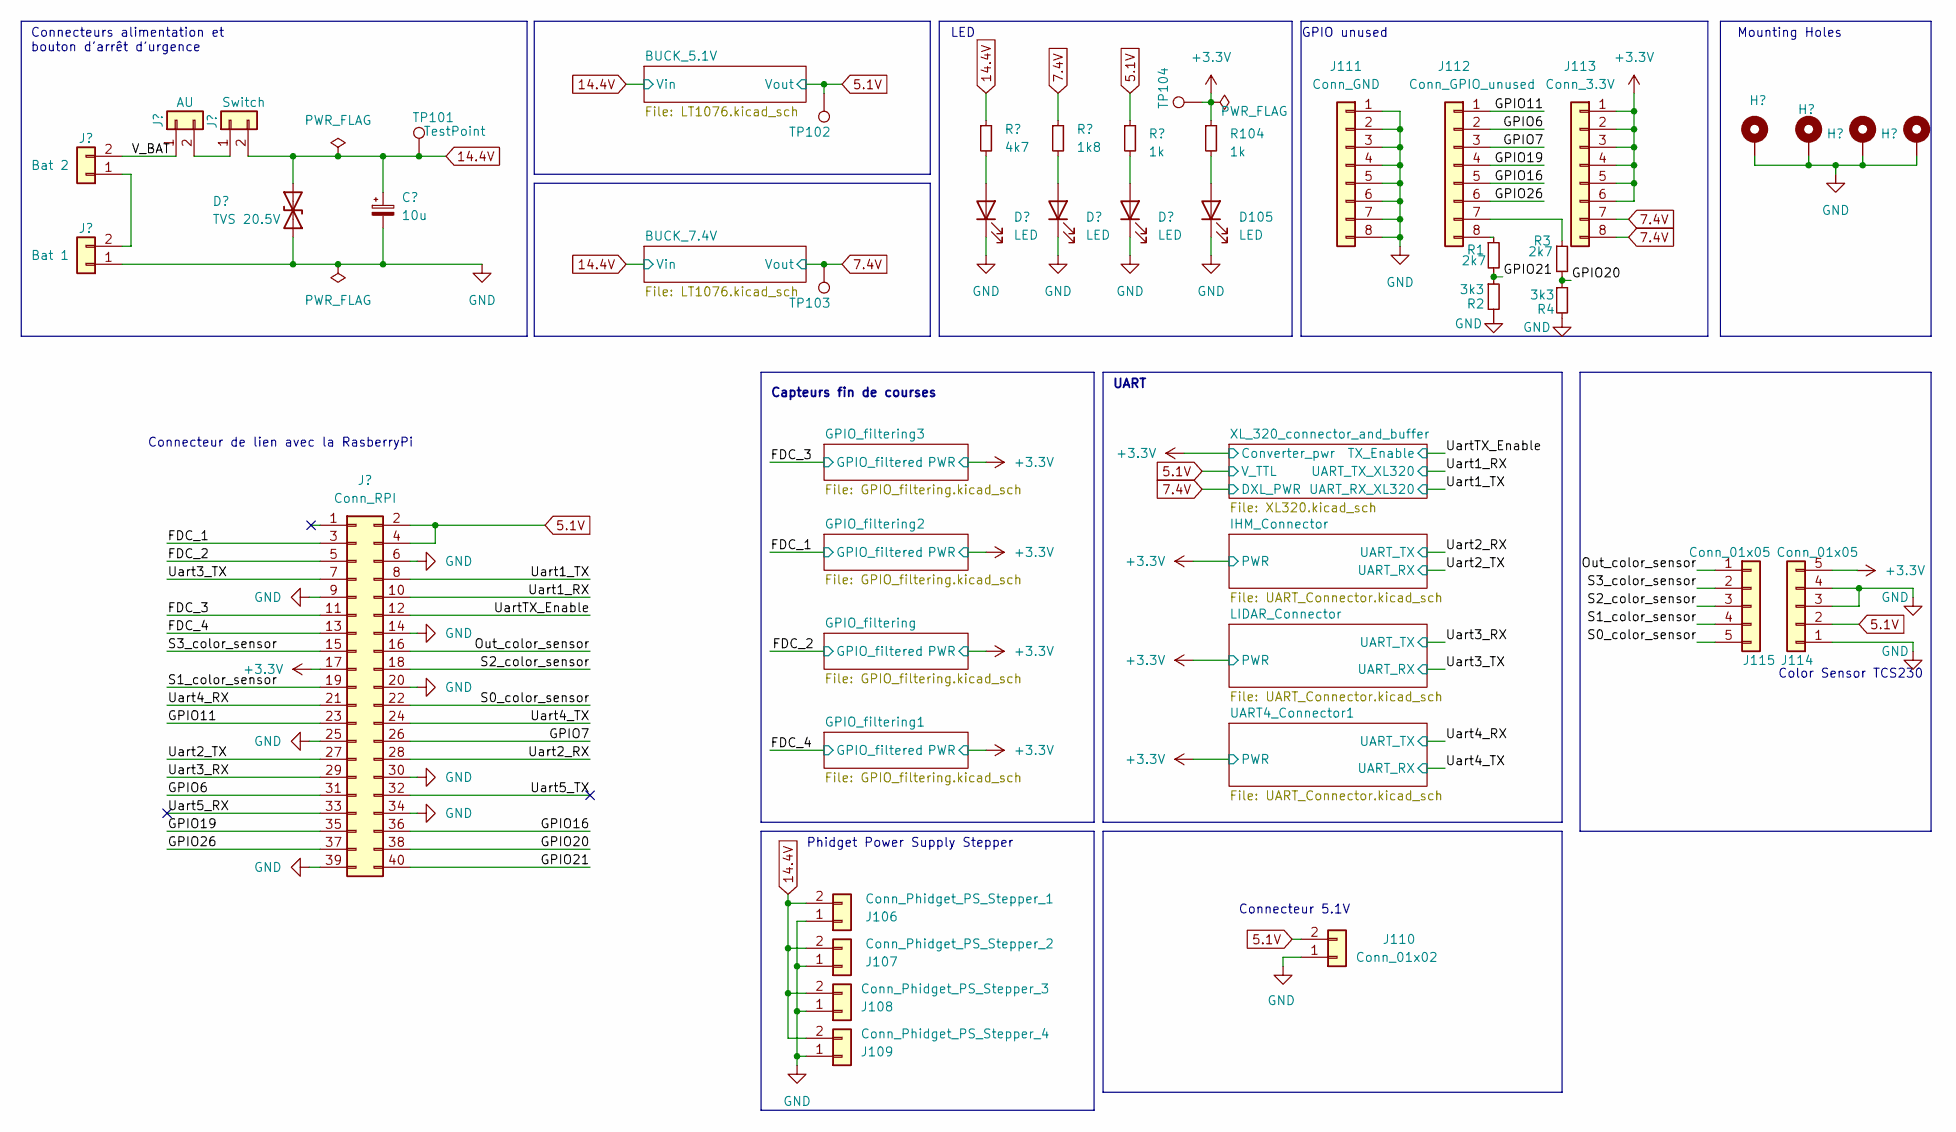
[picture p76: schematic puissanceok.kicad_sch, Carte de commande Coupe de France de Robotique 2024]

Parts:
C101: 10u; CP_Elec_4x5.4; MPN 865060440001
D101: TVS 20.5V; D_SMB; MPN SM6T24A
D102, D103, D104, D105: LED; LED_0603_1608Metric
H101, H102, H103, H104: MountingHole_Pad; MountingHole_2.7mm_M2.5_Pad_Via
J101: Bat 2; 691322110002; MPN 691322110002
J102: Bat 1; 691322110002; MPN 691322110002
J103: AU; 691322110002; MPN 691322110002
J104: Switch; 691322110002; MPN 691322110002
J105: Conn_RPI; PinSocket_2x20_P2.54mm_Vertical
J106: Conn_Phidget_PS_Stepper_1; JST_XH_B2B-XH-A_1x02_P2.50mm_Vertical
J107: Conn_Phidget_PS_Stepper_2; JST_XH_B2B-XH-A_1x02_P2.50mm_Vertical
J108: Conn_Phidget_PS_Stepper_3; JST_XH_B2B-XH-A_1x02_P2.50mm_Vertical
J109: Conn_Phidget_PS_Stepper_4; JST_XH_B2B-XH-A_1x02_P2.50mm_Vertical
J110: Conn_01x02; JST_XH_B2B-XH-A_1x02_P2.50mm_Vertical
J111: Conn_GND; PinHeader_1x08_P2.54mm_Vertical
J112: Conn_GPIO_unused; PinHeader_1x08_P2.54mm_Vertical
J113: Conn_3.3V; PinHeader_1x08_P2.54mm_Vertical
J114, J115: Conn_01x05; JST_XH_B5B-XH-A_1x05_P2.50mm_Vertical
R1, R3: 2k7; R_0402_1005Metric
R2, R4: 3k3; R_0402_1005Metric
R101: 4k7; R_0402_1005Metric
R102: 1k8; R_0402_1005Metric
R103, R104: 1k; R_0402_1005Metric
TP101: TestPoint; Pin_D0.9mm_L10.0mm_W2.4mm_FlatFork
TP102: 5.1V; Pin_D0.9mm_L10.0mm_W2.4mm_FlatFork
TP103: 7.4V; Pin_D0.9mm_L10.0mm_W2.4mm_FlatFork
TP104: 3V3; Pin_D0.9mm_L10.0mm_W2.4mm_FlatFork

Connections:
5.1V: J105.2, J105.4, J110.2, J114.2, R103.1, TP102.1; also elsewhere on the board
7.4V: J113.7, J113.8, R102.1, TP103.1; also elsewhere on the board
14.4V: C101.1, D101.1 (A1), J104.2, J106.2, J107.2, J108.2, J109.2, R101.1, TP101.1; also elsewhere on the board
+3.3V: J105.17, J113.1, J113.2, J113.3, J113.4, J113.5, J113.6, J114.5, R104.1, TP104.1; also elsewhere on the board
/FDC_1: J105.3; also elsewhere on the board
/FDC_2: J105.5; also elsewhere on the board
/FDC_3: J105.11; also elsewhere on the board
/FDC_4: J105.13; also elsewhere on the board
/GPIO6: J105.31, J112.2
/GPIO7: J105.26, J112.3
/GPIO11: J105.23, J112.1
/GPIO16: J105.36, J112.5
/GPIO19: J105.35, J112.4
/GPIO20: J105.38, R3.2, R4.1
/GPIO21: J105.40, R1.2, R2.1
/GPIO26: J105.37, J112.6
/Out_color_sensor: J105.16, J115.1
/S0_color_sensor: J105.22, J115.5
/S1_color_sensor: J105.19, J115.4
/S2_color_sensor: J105.18, J115.3
/S3_color_sensor: J105.15, J115.2
/Uart1_RX: J105.10; also elsewhere on the board
/Uart1_TX: J105.8; also elsewhere on the board
/Uart2_RX: J105.28; also elsewhere on the board
/Uart2_TX: J105.27; also elsewhere on the board
/Uart3_RX: J105.29; also elsewhere on the board
/Uart3_TX: J105.7; also elsewhere on the board
/Uart4_RX: J105.21; also elsewhere on the board
/Uart4_TX: J105.24; also elsewhere on the board
/Uart5_RX: J105.33
/Uart5_TX: J105.32
/UartTX_Enable: J105.12; also elsewhere on the board
/V_BAT: J101.2, J103.1
GND: C101.2, D101.2 (A2), D102.1 (K), D103.1 (K), D104.1 (K), D105.1 (K), H101.1, H102.1, H103.1, H104.1, J102.1, J105.6, J105.9, J105.14, J105.20, J105.25, J105.30, J105.34, J105.39, J106.1, J107.1, J108.1, J109.1, J110.1, J111.1, J111.2, J111.3, J111.4, J111.5, J111.6, J111.7, J111.8, J114.1, J114.3, J114.4, R2.2, R4.2; also elsewhere on the board
unnamed: D102.2 (A), R101.2
unnamed: D103.2 (A), R102.2
unnamed: D104.2 (A), R103.2
unnamed: D105.2 (A), R104.2
unnamed: J101.1, J102.2
unnamed: J103.2, J104.1
unnamed: J112.7, R3.1
unnamed: J112.8, R1.1

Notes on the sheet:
Connecteur 5.1V
Connecteurs alimentation et bouton d'arrêt d'urgence
UART
Mounting Holes
Phidget Power Supply Stepper
Connecteur de lien avec la RasberryPi
Color Sensor TCS230
LED
Capteurs fin de courses
GPIO unused

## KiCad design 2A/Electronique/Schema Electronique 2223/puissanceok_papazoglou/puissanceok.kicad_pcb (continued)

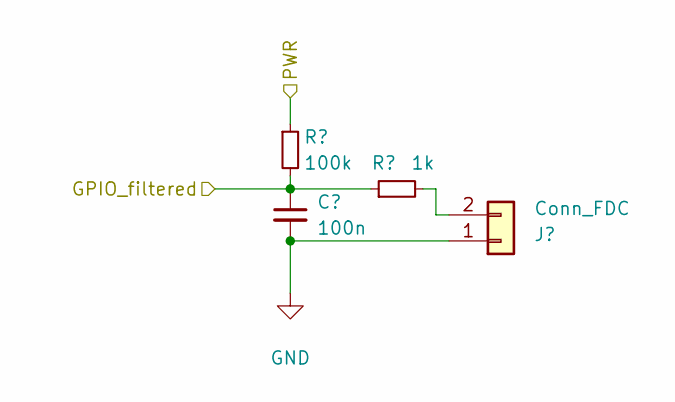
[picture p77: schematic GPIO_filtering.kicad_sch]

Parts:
C201: 100n; C_0402_1005Metric
J201: Conn_FDC; JST_XH_B2B-XH-A_1x02_P2.50mm_Vertical
R201: 100k; R_0402_1005Metric
R202: 1k; R_0402_1005Metric

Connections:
+3.3V: R201.1; also elsewhere on the board
/FDC_1: C201.1, R201.2, R202.1; also elsewhere on the board
GND: C201.2, J201.1; also elsewhere on the board
unnamed: J201.2, R202.2

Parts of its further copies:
C401, C501, C701: 100n; C_0402_1005Metric
J401, J501, J701: Conn_FDC; JST_XH_B2B-XH-A_1x02_P2.50mm_Vertical
R401, R501, R701: 100k; R_0402_1005Metric
R402, R502, R702: 1k; R_0402_1005Metric

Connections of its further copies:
+3.3V: R401.1, R501.1, R701.1; also elsewhere on the board
/FDC_2: C401.1, R401.2, R402.1; also elsewhere on the board
/FDC_3: C501.1, R501.2, R502.1; also elsewhere on the board
/FDC_4: C701.1, R701.2, R702.1; also elsewhere on the board
GND: C401.2, C501.2, C701.2, J401.1, J501.1, J701.1; also elsewhere on the board
unnamed: J401.2, R402.2
unnamed: J501.2, R502.2
unnamed: J701.2, R702.2

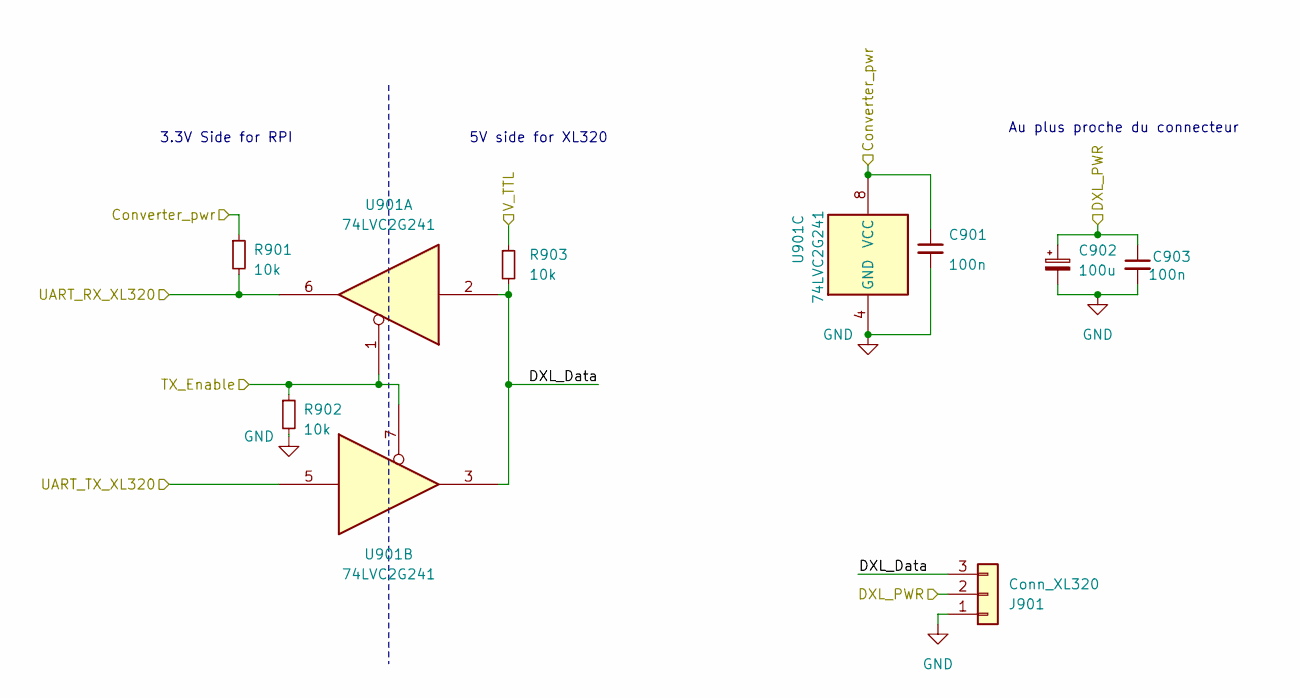
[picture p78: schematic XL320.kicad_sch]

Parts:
C901, C903: 100n; C_0402_1005Metric
C902: 100u; CP_Elec_6.3x7.7; MPN 865060445005
J901: Conn_XL320; JST_XH_B3B-XH-A_1x03_P2.50mm_Vertical
R901, R902, R903: 10k; R_0402_1005Metric
U901: 74LVC2G241; VSSOP-8_2.3x2mm_P0.5mm; MPN 74LVC2G241DC,125

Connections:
5.1V: R903.1; also elsewhere on the board
7.4V: C902.1, C903.1, J901.2; also elsewhere on the board
+3.3V: C901.1, R901.1, U901.8 (VCC); also elsewhere on the board
/Uart1_RX: U901.5; also elsewhere on the board
/Uart1_TX: R901.2, U901.6; also elsewhere on the board
/UartTX_Enable: R902.1, U901.1, U901.7; also elsewhere on the board
/XL_320_connector_and_buffer/DXL_Data: J901.3, R903.2, U901.2, U901.3
GND: C901.2, C902.2, C903.2, J901.1, R902.2, U901.4 (GND); also elsewhere on the board

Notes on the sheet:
3.3V Side for RPI
Au plus proche du connecteur
5V side for XL320

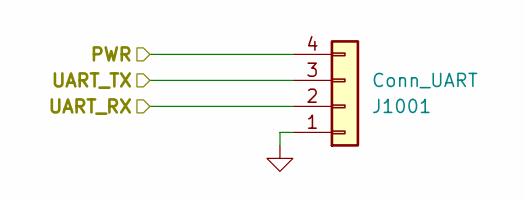
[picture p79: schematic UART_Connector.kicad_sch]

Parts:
J1001: Conn_UART; JST_XH_B4B-XH-A_1x04_P2.50mm_Vertical

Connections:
+3.3V: J1001.4; also elsewhere on the board
/Uart3_RX: J1001.3; also elsewhere on the board
/Uart3_TX: J1001.2; also elsewhere on the board
GND: J1001.1; also elsewhere on the board

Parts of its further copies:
J801, J1101: Conn_UART; JST_XH_B4B-XH-A_1x04_P2.50mm_Vertical

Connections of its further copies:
+3.3V: J801.4, J1101.4; also elsewhere on the board
/Uart2_RX: J801.3; also elsewhere on the board
/Uart2_TX: J801.2; also elsewhere on the board
/Uart4_RX: J1101.3; also elsewhere on the board
/Uart4_TX: J1101.2; also elsewhere on the board
GND: J801.1, J1101.1; also elsewhere on the board

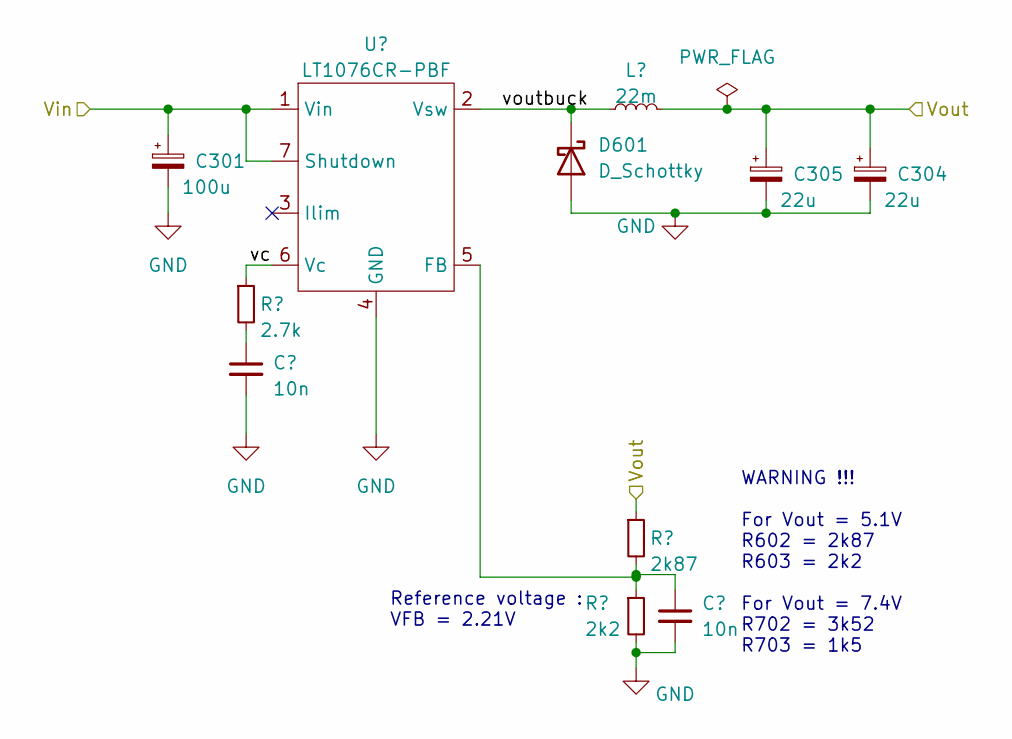
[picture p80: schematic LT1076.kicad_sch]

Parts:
C301: 100u; CP_Elec_6.3x7.7; MPN 865060445005
C302, C303: 10n; C_0402_1005Metric
C304, C305: 22u; CP_Elec_4x5.4; MPN 865060240001
D601: D_Schottky; DST10100S; MPN DST10100S
L301: 22m; L_Changjiang_FNR8065S; MPN 74404084220
R301: 2.7k; R_0402_1005Metric
R302: 2k87; R_0402_1005Metric
R303: 2k2; R_0402_1005Metric
U301: LT1076CR-PBF; TO-263-7_TabPin4; MPN LT1076CR

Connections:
7.4V: C304.1, C305.1, L301.2, R302.1; also elsewhere on the board
14.4V: C301.1, U301.1 (Vin), U301.7 (Shutdown); also elsewhere on the board
/BUCK_7.4V/vc: R301.1, U301.6 (Vc)
GND: C301.2, C302.2, C303.2, C304.2, C305.2, D601.2 (A), R303.2, U301.4 (GND); also elsewhere on the board
unnamed: C302.1, R301.2
unnamed: C303.1, R302.2, R303.1, U301.5 (FB)

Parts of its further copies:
C601: 100u; CP_Elec_6.3x7.7; MPN 865060445005
C602, C603: 10n; C_0402_1005Metric
C604, C605: 22u; CP_Elec_4x5.4; MPN 865060240001
D301: D_Schottky; DST10100S; MPN DST10100S
L601: 22m; L_Changjiang_FNR8065S; MPN 74404084220
R601: 2.7k; R_0402_1005Metric
R602: 2k87; R_0402_1005Metric
R603: 2k2; R_0402_1005Metric
U601: LT1076CR-PBF; TO-263-7_TabPin4; MPN LT1076CR

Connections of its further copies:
5.1V: C604.1, C605.1, L601.2, R602.1; also elsewhere on the board
14.4V: C601.1, U601.1 (Vin), U601.7 (Shutdown); also elsewhere on the board
/BUCK_5.1V/vc: R601.1, U601.6 (Vc)
GND: C601.2, C602.2, C603.2, C604.2, C605.2, D301.2 (A), R603.2, U601.4 (GND); also elsewhere on the board
unnamed: C602.1, R601.2
unnamed: C603.1, R602.2, R603.1, U601.5 (FB)

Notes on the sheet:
Reference voltage : VFB = 2.21V
WARNING !!! For Vout = 5.1V R602 = 2k87 R603 = 2k2 For Vout = 7.4V R702 = 3k52 R703 = 1k5

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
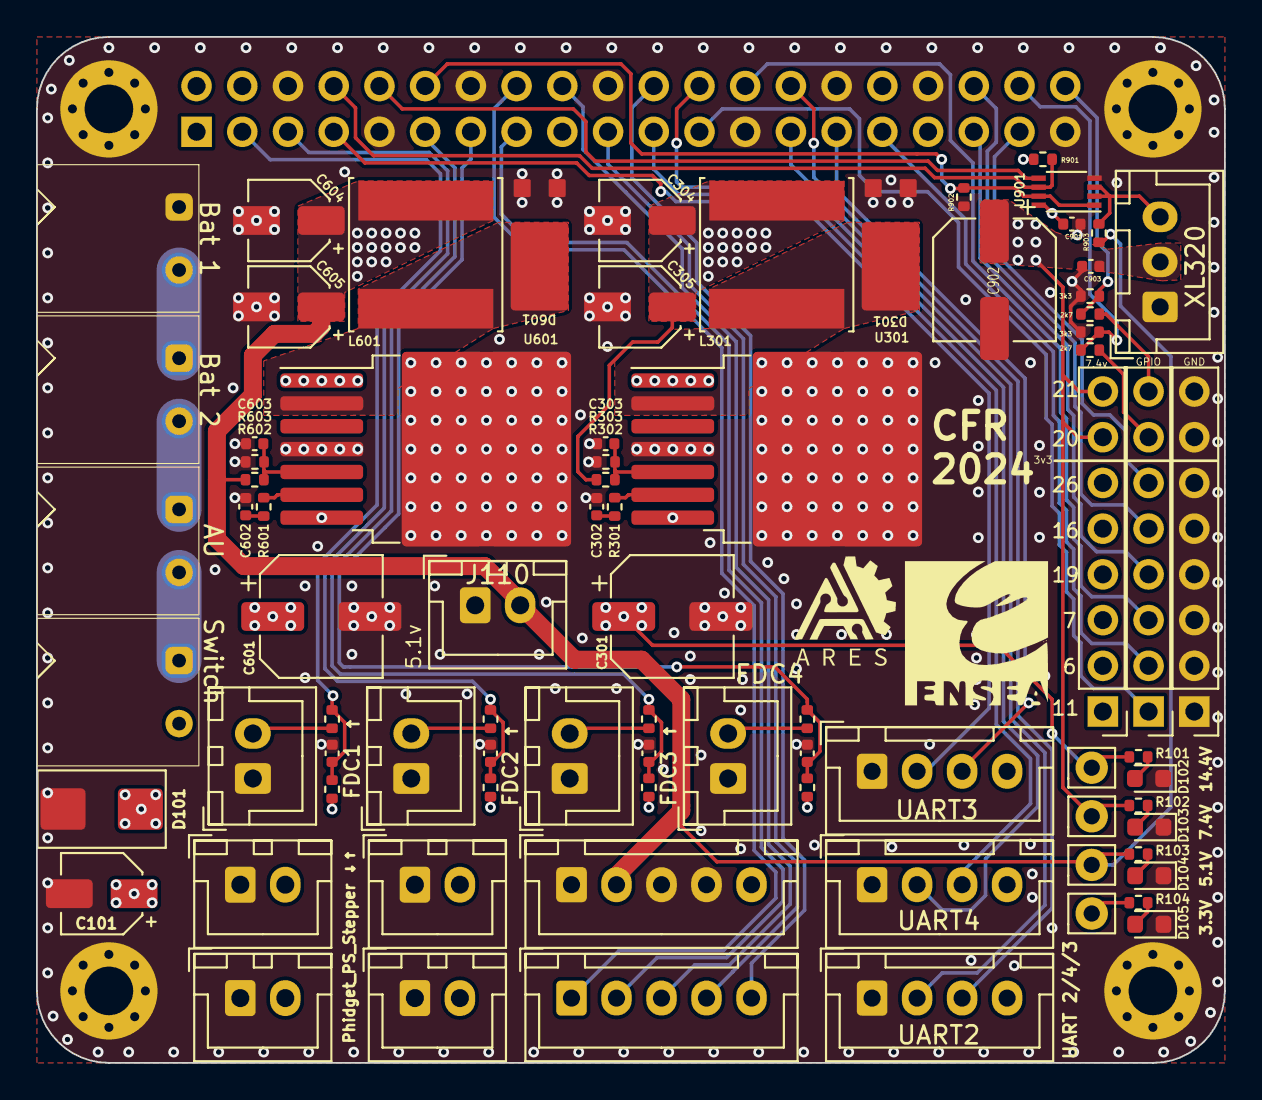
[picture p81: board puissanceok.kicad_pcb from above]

Board: 4 copper layers, 66.0 x 57.0 mm, 86 parts (1 on the bottom side), 53 nets.

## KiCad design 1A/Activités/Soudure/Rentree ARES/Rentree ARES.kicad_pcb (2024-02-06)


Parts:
F2, F3: Fuse; Fuse_internal_trace
J1: Conn_01x10_Female; PinHeader_1x10_P2.54mm_Horizontal
TP1, TP2, TP3, TP4: TestPoint_Small; TestPoint_Pad_D1.5mm

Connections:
+3.3V: J1.1; also elsewhere on the board
/BUZZER: J1.4; also elsewhere on the board
/OSC: J1.3; also elsewhere on the board
/RST: J1.9; also elsewhere on the board
/S1: J1.2; also elsewhere on the board
/Simon un peu plus dur/LED0: J1.5; also elsewhere on the board
/Simon un peu plus dur/LED1: J1.6; also elsewhere on the board
/Simon un peu plus dur/SW0: F2.1, TP1.1; also elsewhere on the board
/Simon un peu plus dur/SW1: F3.1, TP2.1; also elsewhere on the board
GND: J1.10; also elsewhere on the board
unnamed: F2.2, J1.7, TP4.1
unnamed: F3.2, J1.8, TP3.1


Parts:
A1: Arduino_UNO_R3

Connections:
+3.3V: A1.4 (3V3); also elsewhere on the board
/BUZZER: A1.25 (D10); also elsewhere on the board
/RST: A1.28 (D13); also elsewhere on the board
/Simon un peu plus dur/LED0: A1.9 (A0); also elsewhere on the board
/Simon un peu plus dur/LED1: A1.27 (D12); also elsewhere on the board
/Simon un peu plus dur/SW0: A1.23 (D8); also elsewhere on the board
/Simon un peu plus dur/SW1: A1.24 (D9); also elsewhere on the board
GND: A1.6 (GND), A1.7 (GND), A1.29 (GND); also elsewhere on the board


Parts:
D3, D4: LED; LED_D5.0mm_Clear
LS1: Speaker; MagneticBuzzer_ProSignal_ABT-410-RC
R8, R9: 470; R_0805_2012Metric
R10, R11: 100k; R_0805_2012Metric
SW1, SW2: SW_SPST; SW_PUSH_6mm_H5mm

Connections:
+3.3V: D3.2 (A), D4.2 (A), LS1.1, R10.1, R11.1; also elsewhere on the board
/BUZZER: LS1.2; also elsewhere on the board
/Simon un peu plus dur/LED0: R8.2; also elsewhere on the board
/Simon un peu plus dur/LED1: R9.2; also elsewhere on the board
/Simon un peu plus dur/SW0: R11.2, SW1.2 (B); also elsewhere on the board
/Simon un peu plus dur/SW1: R10.2, SW2.2 (B); also elsewhere on the board
GND: SW1.1 (A), SW2.1 (A); also elsewhere on the board
unnamed: D3.1 (K), R8.1
unnamed: D4.1 (K), R9.1


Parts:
C1, C2: 10µF; C_1206_3216Metric
D1, D2: LED; LED_D5.0mm_Clear
F1: Fuse; Fuse_trace
Q1, Q2: Q_NPN_EBC; TO-92_Inline
R4, R7: 560; R_0805_2012Metric
R5, R6: 47k; R_0805_2012Metric

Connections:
+3.3V: R4.1, R5.1, R6.1, R7.1; also elsewhere on the board
/OSC: C2.1, D2.1 (K), Q2.3 (C); also elsewhere on the board
GND: F1.2, Q1.1 (E), Q2.1 (E); also elsewhere on the board
unnamed: C1.1, Q2.2 (B), R5.2
unnamed: C1.2, D1.1 (K), F1.1, Q1.3 (C)
unnamed: C2.2, Q1.2 (B), R6.2
unnamed: D1.2 (A), R4.2
unnamed: D2.2 (A), R7.2

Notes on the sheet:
LED simple
Fusible à découper au cutter
On fera pulser l'alim pour s'assurer que la led vient pas d'ailleurs


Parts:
R1: 3.3k; R_Axial_DIN0207_L6.3mm_D2.5mm_P2.54mm_Vertical
R2: 33k; R_Axial_DIN0207_L6.3mm_D2.5mm_P10.16mm_Horizontal
R3: 4.7k; R_Axial_DIN0207_L6.3mm_D2.5mm_P10.16mm_Horizontal

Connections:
+3.3V: R1.1; also elsewhere on the board
/S1: R2.2, R3.1; also elsewhere on the board
GND: R3.2; also elsewhere on the board
unnamed: R1.2, R2.1

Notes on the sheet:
2 Top 1 bottom


Board: 4 copper layers, 57.0 x 56.2 mm, 31 parts (0 on the bottom side), 20 nets.

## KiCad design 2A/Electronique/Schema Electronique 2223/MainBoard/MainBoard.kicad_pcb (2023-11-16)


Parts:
ARU1: 180G-2
BAT1, BAT2: 180G-2
C3: C_Polarized_Small; E5-6
D4: 4V7; D_0603_1608Metric; Mouser Part Number 771-BZX84J-C4V7115
D5: 1.5SMBJ36CA; D_SMB; Mouser Part Number 652-1.5SMBJ36CA-H
F1: 15A; Fuse_1206_3216Metric_Pad1.42x1.75mm_HandSolder; Mouser Part Number 693-3413.0330.22
F2: 10A; Fuse_1206_3216Metric_Pad1.42x1.75mm_HandSolder; Mouser Part Number 530-0685P9100-01
LED3: LG_R971; LEDC2012X90N
PWROUT1: 180G-2
Q3: PMOS; MOS_WDFN8; Mouser Part Number 863-NTTFS015P03P8ZWG
R18: 680; R_0805_2012Metric_Pad1.20x1.40mm_HandSolder
R19: 10k; R_0805_2012Metric_Pad1.20x1.40mm_HandSolder
U4: TSR_1-2450; TSR-1-24120

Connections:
+5V: U4.3 (VOUT+); also elsewhere on the board
GND: BAT2.2, C3.2, C3.-, D5.1 (A1), LED3.1 (K), PWROUT1.1, R19.2, U4.2 (GND); also elsewhere on the board
unnamed: ARU1.1, F1.2
unnamed: BAT1.1, F1.1
unnamed: BAT1.2, BAT2.1
unnamed: D4.2 (A), Q3.1 (G), R19.1
unnamed: ARU1.2, D5.2 (A2), Q3.2 (D)
unnamed: F2.2, PWROUT1.2
unnamed 37: LED3.2 (A), R18.2; also elsewhere on the board
VBAT: C3.1, C3.+, D4.1 (K), F2.1, Q3.3 (S), R18.1, U4.1 (VIN+); also elsewhere on the board

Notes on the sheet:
Power Supply led
Power output
CON BAT
Power input Fuse + emergency stop button + ESD/reverse polarity protection
5V regulator


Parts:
CAN1: Conn_01x03_Male; JST_XH_B3B-XH-A_1x03_P2.50mm_Vertical
D1, D2, D3: ESD7C5.0DT5G; SOT-416; Mouser Part Number 863-ESD7C5.0DT5G
I2C_ext1: Conn_01x03_Male; JST_XH_B3B-XH-A_1x03_P2.50mm_Vertical
J1, J2, J3, J4: Screw_Terminal_01x01; MountingHole_4.3mm_M4_ISO7380_Pad
JP1, JP2, JP3: Jumper_3_Open; PinHeader_1x03_P2.54mm_Vertical
LED1, LED2: LG_R971; LEDC2012X90N
R1, R2, R3, R4, R5, R6, R9, R10, R11: 1k; R_0805_2012Metric_Pad1.20x1.40mm_HandSolder
R7, R8: 100; R0805
SPI_ext1: Conn_01x05_Male; JST_XH_B5B-XH-A_1x05_P2.50mm_Vertical
TOF_AR1, TOF_AR2: Conn_01x06_Male; JST_XH_B6B-XH-A_1x06_P2.50mm_Vertical
TOF_AV1, TOF_AV2: Conn_01x06_Male; JST_XH_B6B-XH-A_1x06_P2.50mm_Vertical
Tirette1: Conn_01x02_Male; PinHeader_1x02_P2.54mm_Vertical
U1: NUCLEO_F446RE; MB1136
UART4, UART5, UART6: Conn_01x04_Male; JST_XH_B4B-XH-A_1x04_P2.50mm_Vertical

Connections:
+3.3V: JP1.3 (B), JP2.3 (B), JP3.3 (B), R9.1, R10.1, TOF_AR1.1, TOF_AR2.1, TOF_AV1.1, TOF_AV2.1, U1.+3V3
+5V: JP1.1 (A), JP2.1 (A), JP3.1 (A), Tirette1.1, U1.E5V; also elsewhere on the board
CAN1_RX: CAN1.1, U1.PA11
CAN1_TX: CAN1.2, U1.PA12
COD_DROITE_A: U1.PA9; also elsewhere on the board
COD_DROITE_B: U1.PA8; also elsewhere on the board
COD_GAUCHE_A: U1.PA6; also elsewhere on the board
COD_GAUCHE_B: U1.PA7; also elsewhere on the board
DIR_D: U1.PC11; also elsewhere on the board
DIR_G: U1.PC2; also elsewhere on the board
EN_D: U1.PC1; also elsewhere on the board
EN_G: U1.PC0; also elsewhere on the board
GND: CAN1.3, D1.3 (A), D2.3 (A), D3.3 (A), I2C_ext1.3, J1.1, J2.1, J3.1, J4.1, LED1.1 (K), LED2.1 (K), R11.2, SPI_ext1.5, TOF_AR1.2, TOF_AR2.2, TOF_AV1.2, TOF_AV2.2, U1.AGND, U1.GND1, U1.GND2, U1.GND3, U1.GND4, U1.GND5, U1.GND6, UART4.4, UART5.4, UART6.4; also elsewhere on the board
LED1: R7.1, U1.PA15
LED2: R8.1, U1.PC13
unnamed: JP1.2 (C), R1.1, R2.1
unnamed: JP2.2 (C), R3.1, R4.1
unnamed: JP3.2 (C), R5.1, R6.1
unnamed: LED1.2 (A), R7.2
unnamed: LED2.2 (A), R8.2
RX1: D1.2 (K2), R2.2, U1.PA1, UART4.3
RX2: D2.2 (K2), R4.2, U1.PD2, UART5.3
RX3: D3.2 (K2), R6.2, U1.PC7, UART6.3
SCL1: I2C_ext1.1, R9.2, TOF_AR1.4, TOF_AR2.4, TOF_AV1.4, TOF_AV2.4, U1.PB6
SDA1: I2C_ext1.2, R10.2, TOF_AR1.3, TOF_AR2.3, TOF_AV1.3, TOF_AV2.3, U1.PB7
SPI2_CS: SPI_ext1.2, U1.PA10
SPI2_MISO: SPI_ext1.4, U1.PB14
SPI2_MOSI: SPI_ext1.1, U1.PC3
SPI2_SCK: SPI_ext1.3, U1.PB13
STEP_D: U1.PC9; also elsewhere on the board
STEP_G: U1.PB9; also elsewhere on the board
TIRETTE: R11.1, Tirette1.2, U1.PC8
TOF_IT_AR: TOF_AR1.6, TOF_AR2.6, U1.PB15
TOF_IT_AV: TOF_AV1.6, TOF_AV2.6, U1.PB1
TX1: D1.1 (K1), R1.2, U1.PA0, UART4.2
TX2: D2.1 (K1), R3.2, U1.PC12, UART5.2
TX3: D3.1 (K1), R5.2, U1.PC6, UART6.2
VBAT: UART4.1, UART5.1, UART6.1; also elsewhere on the board
XSHUT1: TOF_AV1.5, U1.PB2
XSHUT2: TOF_AV2.5, U1.PB10
XSHUT3: TOF_AR1.5, U1.PB4
XSHUT4: TOF_AR2.5, U1.PB5

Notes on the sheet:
UART
NUCLEO F446RE
Ext SPI/I2C/CAN
TOF sensors
TIRETTE

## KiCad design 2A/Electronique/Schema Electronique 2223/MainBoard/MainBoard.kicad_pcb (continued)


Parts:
L_ENCODER1: Conn_01x05_Male; JST_XH_B5B-XH-A_1x05_P2.50mm_Vertical
R14, R15, R16, R17: 4k; R_0805_2012Metric_Pad1.20x1.40mm_HandSolder
R_ENCODER1: Conn_01x05_Male; JST_XH_B5B-XH-A_1x05_P2.50mm_Vertical

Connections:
+5V: L_ENCODER1.1, R14.1, R15.1, R16.1, R17.1, R_ENCODER1.1; also elsewhere on the board
COD_DROITE_A: R16.2, R_ENCODER1.3; also elsewhere on the board
COD_DROITE_B: R17.2, R_ENCODER1.4; also elsewhere on the board
COD_GAUCHE_A: L_ENCODER1.3, R14.2; also elsewhere on the board
COD_GAUCHE_B: L_ENCODER1.4, R15.2; also elsewhere on the board
GND: L_ENCODER1.2, L_ENCODER1.5, R_ENCODER1.2, R_ENCODER1.5; also elsewhere on the board

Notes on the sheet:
Codeur Droite
Left Encoder
Right Encoder


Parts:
C1, C2: 100µ; E5-6
JP5, JP6, JP7, JP8, JP9, JP10: Jumper_2_Open; PinHeader_1x02_P2.54mm_Vertical
LSTEP1: Conn_01x04_Male; JST_XH_B4B-XH-A_1x04_P2.50mm_Vertical
Q1: PMOS; MOS_WDFN8; Mouser Part Number 863-NTTFS015P03P8ZWG
Q2: MBT3906DW1; SOT-363_SC-70-6; Mouser Part Number 863-MBT3906DW1T1G
R12, R13: 10k; R_0805_2012Metric_Pad1.20x1.40mm_HandSolder
RSTEP1: Conn_01x04_Male; JST_XH_B4B-XH-A_1x04_P2.50mm_Vertical
U2, U3: POLOLU_DRV8825

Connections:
+5V: JP5.1 (A), JP6.1 (A), JP7.1 (A), JP8.1 (A), JP9.1 (A), JP10.1 (A), U2.RST/ (RST), U2.SLP/ (SLP), U3.RST/ (RST), U3.SLP/ (SLP); also elsewhere on the board
/Motorisation/A1_L: LSTEP1.2, U2.A1
/Motorisation/A1_R: RSTEP1.2, U3.A1
/Motorisation/A2_L: LSTEP1.1, U2.A2
/Motorisation/A2_R: RSTEP1.1, U3.A2
/Motorisation/Vmot: C1.+, C2.+, Q1.3 (S), Q2.1 (E1), U2.VMOT, U3.VMOT
DIR_D: U3.DIR; also elsewhere on the board
DIR_G: U2.DIR; also elsewhere on the board
EN_D: U3.EN/ (EN); also elsewhere on the board
EN_G: U2.EN/ (EN); also elsewhere on the board
GND: C1.-, C2.-, R12.2, R13.2, U2.GND1, U2.GND2, U3.GND1, U3.GND2; also elsewhere on the board
unnamed: JP5.2 (B), U2.M0
unnamed: JP6.2 (B), U2.M1
unnamed: JP7.2 (B), U2.M2
unnamed: JP8.2 (B), U3.M0
unnamed: JP9.2 (B), U3.M1
unnamed: JP10.2 (B), U3.M2
unnamed: LSTEP1.3, U2.B1
unnamed: LSTEP1.4, U2.B2
unnamed: Q1.1 (G), Q2.6 (C1), R13.1
unnamed: Q2.2 (B1), Q2.3 (C2), Q2.5 (B2), R12.1
unnamed: RSTEP1.3, U3.B1
unnamed: RSTEP1.4, U3.B2
STEP_D: U3.STEP; also elsewhere on the board
STEP_G: U2.STEP; also elsewhere on the board
VBAT: Q1.2 (D), Q2.4 (E2); also elsewhere on the board

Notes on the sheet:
Back-EMF blocking ideal diode
Right Stepper Driver
Left Stepper Driver



Board: 2 copper layers, 103.6 x 98.5 mm, 70 parts (23 on the bottom side), 66 nets.

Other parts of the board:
PWR: LG_R971; LEDC2012X90N

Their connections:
GND: PWR.1 (K); also elsewhere on the board
unnamed 37: PWR.2 (A); also elsewhere on the board

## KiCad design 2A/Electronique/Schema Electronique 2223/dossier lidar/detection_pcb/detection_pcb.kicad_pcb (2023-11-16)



Board: 2 copper layers, 96.0 x 96.0 mm, 145 parts (40 on the bottom side), 80 nets.

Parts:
C1: 10u; C_0805_2012Metric_Pad1.18x1.45mm_HandSolder
C2: 22u; C_0805_2012Metric_Pad1.18x1.45mm_HandSolder
C3, C4, C5, C6, C7, C8, C9, C10, C11, C12, C13, C14, C15, C16, C17, C18: 1u; C_0805_2012Metric_Pad1.18x1.45mm_HandSolder
C19: 4.7u; C_0805_2012Metric_Pad1.18x1.45mm_HandSolder
C20, C21, C22: 100n; C_0805_2012Metric_Pad1.18x1.45mm_HandSolder
C23, C24: 20p; C_0603_1608Metric_Pad1.08x0.95mm_HandSolder
D1: 4V7; D_0603_1608Metric
D2: 1.5SMBJ36CA; D_SMB
D3: ESD7C5.0DT5G; SOT-416
F1: polyfuse; polyswitch
H1, H2, H3, H4: MountingHole_Pad; MountingHole_4.3mm_M4_DIN965_Pad
J1: BAT; JST_XH_B2B-XH-A_1x02_P2.50mm_Vertical
JP1: SolderJumper_2_Open; SolderJumper-2_P1.3mm_Open_TrianglePad1.0x1.5mm
LED1, LED2, LED3, LED4, LED5, LED6, LED7, LED8, LED9, LED10, LED11, LED12, LED13, LED14, LED15, LED16: LED; LED_D3.0mm
Q1: PMOS; SOT-23
R1, R2, R3, R4, R5, R6, R7, R8, R9, R10, R11, R12, R13, R14, R15, R16, R17, R18, R19, R20, R21, R22, R23, R24, R25, R26, R27, R28, R29, R30, R31, R32, R33: 10k; R_0805_2012Metric_Pad1.20x1.40mm_HandSolder
R34, R35: 2.2k; R_0805_2012Metric
R36, R37: DNP; R_0805_2012Metric
R38, R39, R40, R41, R42, R43, R44, R45, R46, R47, R48, R49, R50, R51, R52, R53: 3k; R_0805_2012Metric_Pad1.20x1.40mm_HandSolder
RX1: TestPoint; TestPoint_Pad_D1.0mm
SCL1: TestPoint; TestPoint_Pad_D1.0mm
SDA1: TestPoint; TestPoint_Pad_D1.0mm
SWD1: Conn_02x07_Odd_Even; PinHeader_2x07_P1.27mm_Vertical_SMD
TX1: TestPoint; TestPoint_Pad_D1.0mm
U1: Buck_3.3V; PinHeader_1x03_P2.54mm_Vertical
U2, U3, U4, U5, U6, U7, U8, U9, U10, U11, U12, U13, U14, U15, U16, U17: VL53L1X_module; PinHeader_2x05_P2.54mm_Vertical
U18: STM32G070; LQFP-64_10x10mm_P0.5mm
UART1: Conn_01x02_Male; JST_XH_B2B-XH-A_1x02_P2.50mm_Vertical
XSDN1, XSDN2, XSDN3, XSDN4, XSDN5, XSDN6, XSDN7, XSDN8, XSDN9, XSDN10, XSDN11, XSDN12, XSDN13, XSDN14, XSDN15, XSDN16: TestPoint; TestPoint_Pad_D1.0mm
Y1: 16MHz; Crystal_SMD_EuroQuartz_MT-4Pin_3.2x2.5mm

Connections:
+3V3: C1.1, C3.1, C4.1, C5.1, C6.1, C7.1, C8.1, C9.1, C10.1, C11.1, C12.1, C13.1, C14.1, C15.1, C16.1, C17.1, C18.1, C19.1, C20.1, C21.1, JP1.1 (A), LED1.2 (A), LED2.2 (A), LED3.2 (A), LED4.2 (A), LED5.2 (A), LED6.2 (A), LED7.2 (A), LED8.2 (A), LED9.2 (A), LED10.2 (A), LED11.2 (A), LED12.2 (A), LED13.2 (A), LED14.2 (A), LED15.2 (A), LED16.2 (A), R2.2, R3.2, R4.2, R5.2, R6.2, R7.2, R8.2, R9.2, R10.2, R11.2, R12.2, R13.2, R14.2, R15.2, R16.2, R17.2, R18.2, R19.2, R20.2, R21.2, R22.2, R23.2, R24.2, R25.2, R26.2, R27.2, R28.2, R29.2, R30.2, R31.2, R32.2, R33.2, R34.1, R35.2, R36.1, R37.1, U1.3 (VOUT), U2.5 (VDD), U3.5 (VDD), U4.5 (VDD), U5.5 (VDD), U6.5 (VDD), U7.5 (VDD), U8.5 (VDD), U9.5 (VDD), U10.5 (VDD), U11.5 (VDD), U12.5 (VDD), U13.5 (VDD), U14.5 (VDD), U15.5 (VDD), U16.5 (VDD), U17.5 (VDD), U18.6 (VBAT), U18.7 (VREF+), U18.8 (VDD/VDDA)
GND: C1.2, C2.2, C3.2, C4.2, C5.2, C6.2, C7.2, C8.2, C9.2, C10.2, C11.2, C12.2, C13.2, C14.2, C15.2, C16.2, C17.2, C18.2, C19.2, C20.2, C21.2, C22.1, C23.2, C24.2, D2.2 (A2), D3.3 (A), H1.1, H2.1, H3.1, H4.1, J1.2, R1.2, SWD1.5, SWD1.7, SWD1.11, U1.2 (GND), U2.6 (GND), U2.9 (NC1), U3.6 (GND), U3.9 (NC1), U4.6 (GND), U4.9 (NC1), U5.6 (GND), U5.9 (NC1), U6.6 (GND), U6.9 (NC1), U7.6 (GND), U7.9 (NC1), U8.6 (GND), U8.9 (NC1), U9.6 (GND), U9.9 (NC1), U10.6 (GND), U10.9 (NC1), U11.6 (GND), U11.9 (NC1), U12.6 (GND), U12.9 (NC1), U13.6 (GND), U13.9 (NC1), U14.6 (GND), U14.9 (NC1), U15.6 (GND), U15.9 (NC1), U16.6 (GND), U16.9 (NC1), U17.6 (GND), U17.9 (NC1), U18.9 (VSS/VSSA), Y1.2, Y1.4
INT0: R2.1, U2.1 (INT), U18.14 (PC1)
INT1: R5.1, U3.1 (INT), U18.4 (PC14)
INT2: R6.1, U4.1 (INT), U18.1 (PC11)
INT3: R9.1, U5.1 (INT), U18.62 (PB8)
INT4: R11.1, U6.1 (INT), U18.59 (PB5)
INT5: R10.1, U7.1 (INT), U18.54 (PD4)
INT6: R15.1, U8.1 (INT), U18.51 (PD1)
INT7: R14.1, U9.1 (INT), U18.48 (PC8)
INT8: R19.1, U10.1 (INT), U18.41 (PD9)
INT9: R18.1, U11.1 (INT), U18.38 (PC6)
INT10: R23.1, U12.1 (INT), U18.35 (PB15)
INT11: R22.1, U13.1 (INT), U18.32 (PB12)
INT12: R27.1, U14.1 (INT), U18.29 (PB2)
INT13: R26.1, U15.1 (INT), U18.26 (PC5)
INT14: R31.1, U16.1 (INT), U18.23 (PA6)
INT15: R30.1, U17.1 (INT), U18.20 (PA3)
LED0: R38.1, U18.16 (PC3)
LED1: R39.2, U18.13 (PC0)
LED2: R40.2, U18.3 (PC13)
LED3: R41.2, U18.64 (PC10)
LED4: R42.2, U18.61 (PB7)
LED5: R43.2, U18.58 (PB4)
LED6: R44.2, U18.53 (PD3)
LED7: R45.2, U18.50 (PD0)
LED8: R46.2, U18.47 (PA15)
LED9: R47.2, U18.40 (PD8)
LED10: R48.2, U18.43 (PA11)
LED11: R49.2, U18.34 (PB14)
LED12: R50.2, U18.31 (PB11)
LED13: R51.2, U18.28 (PB1)
LED14: R52.2, U18.25 (PC4)
LED15: R53.2, U18.22 (PA5)
NRST: C22.2, SWD1.12, U18.12 (NRST)
unnamed: D1.2 (A), Q1.1 (G), R1.1
unnamed: C2.1, D1.1 (K), Q1.3 (S), U1.1 (VIN)
unnamed: D2.1 (A1), F1.1, Q1.2 (D)
unnamed: F1.2, J1.1
unnamed: JP1.2 (B), SWD1.3
unnamed: LED1.1 (K), R38.2
unnamed: LED2.1 (K), R39.1
unnamed: LED3.1 (K), R40.1
unnamed: LED4.1 (K), R41.1
unnamed: LED5.1 (K), R42.1
unnamed: LED6.1 (K), R43.1
unnamed: LED7.1 (K), R44.1
unnamed: LED8.1 (K), R45.1
unnamed: LED9.1 (K), R46.1
unnamed: LED10.1 (K), R47.1
unnamed: LED11.1 (K), R48.1
unnamed: LED12.1 (K), R49.1
unnamed: LED13.1 (K), R50.1
unnamed: LED14.1 (K), R51.1
unnamed: LED15.1 (K), R52.1
unnamed: LED16.1 (K), R53.1
unnamed: C23.1, U18.10 (PF0), Y1.1
unnamed: C24.1, U18.11 (PF1), Y1.3
RX: D3.1 (K), R37.2, RX1.1, U18.56 (PD6), UART1.2
SCL: R35.1, SCL1.1, U2.2 (SCL), U3.2 (SCL), U4.2 (SCL), U5.2 (SCL), U6.2 (SCL), U7.2 (SCL), U8.2 (SCL), U9.2 (SCL), U10.2 (SCL), U11.2 (SCL), U12.2 (SCL), U13.2 (SCL), U14.2 (SCL), U15.2 (SCL), U16.2 (SCL), U17.2 (SCL), U18.37 (PA9)
SDA: R34.2, SDA1.1, U2.4 (SDA), U3.4 (SDA), U4.4 (SDA), U5.4 (SDA), U6.4 (SDA), U7.4 (SDA), U8.4 (SDA), U9.4 (SDA), U10.4 (SDA), U11.4 (SDA), U12.4 (SDA), U13.4 (SDA), U14.4 (SDA), U15.4 (SDA), U16.4 (SDA), U17.4 (SDA), U18.42 (PA10)
SWCLK: SWD1.6, U18.46 (BOOT0-PA14)
SWDIO: SWD1.4, U18.45 (PA13)
TX: D3.2 (K), R36.2, TX1.1, U18.55 (PD5), UART1.1
XSDN1: R3.1, U2.3 (XSDN), U18.15 (PC2), XSDN7.1
XSDN2: R4.1, U3.3 (XSDN), U18.5 (PC15), XSDN16.1
XSDN3: R7.1, U4.3 (XSDN), U18.2 (PC12), XSDN14.1
XSDN4: R8.1, U5.3 (XSDN), U18.63 (PB9), XSDN12.1
XSDN5: R12.1, U6.3 (XSDN), U18.60 (PB6), XSDN9.1
XSDN6: R13.1, U7.3 (XSDN), U18.57 (PB3), XSDN8.1
XSDN7: R16.1, U8.3 (XSDN), U18.52 (PD2), XSDN2.1
XSDN8: R17.1, U9.3 (XSDN), U18.49 (PC9), XSDN11.1
XSDN9: R20.1, U10.3 (XSDN), U18.44 (PA12), XSDN5.1
XSDN10: R21.1, U11.3 (XSDN), U18.39 (PC7), XSDN10.1
XSDN11: R24.1, U12.3 (XSDN), U18.36 (PA8), XSDN4.1
XSDN12: R25.1, U13.3 (XSDN), U18.33 (PB13), XSDN15.1
XSDN13: R28.1, U14.3 (XSDN), U18.30 (PB10), XSDN13.1
XSDN14: R29.1, U15.3 (XSDN), U18.27 (PB0), XSDN6.1
XSDN15: R32.1, U16.3 (XSDN), U18.24 (PA7), XSDN3.1
XSDN16: R33.1, U17.3 (XSDN), U18.21 (PA4), XSDN1.1

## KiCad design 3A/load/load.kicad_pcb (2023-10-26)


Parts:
C1, C8, C9, C12, C16: 100n; C_0402_1005Metric
C2, C3, C4: 10u; C_0805_2012Metric
C5, C7, C19, C20: C_Small; C_0402_1005Metric
C6, C10, C11: 1u; C_0402_1005Metric
C13: 100p; C_0402_1005Metric
C14: 2.2u; C_0603_1608Metric
C15: 1n; C_0402_1005Metric
C17, C18: 22u; C_0805_2012Metric
F1: 25A; Fuse_1206_3216Metric; Mouser Part Number 652-SF-1206HV25M-2
H1, H2, H3, H4: M4; MountingHole_4.3mm_M4_Pad_Via
J1, J2: Screw_Terminal_01x02; TerminalBlock_TE_282834-2_1x02_P2.54mm_Horizontal
J3: JST_XH_B10B-XH-A_1x10_P2.50mm_Vertical
L1: 1u; L_0603_1608Metric
NTC1: Conn_01x02_Socket; JST_XH_B2B-XH-A_1x02_P2.50mm_Vertical
Q1: PMBT2222A; SOT-23; Mouser Part Number 771-PMBT2222A-T/R
Q2: IXTH64N10L2; TO-247-3_Vertical; Mouser Part Number 747-IXTH64N10L2
R1, R2, R3, R4, R5, R13: R_Small; R_0402_1005Metric
R6: 2R; R_0805_2012Metric
R7, R10, R12: 1k; R_0402_1005Metric
R8: 10k; R_0402_1005Metric
R9: 0R; R_0805_2012Metric
R11: 100R; R_0805_2012Metric
Rs1, Rs2, Rs3, Rs4, Rs5: 50m; R_1206_3216Metric; Mouser Part Number 504-MSMA1206R0500FCM
U1: LMC7660; SOIC-8_3.9x4.9mm_P1.27mm; Mouser Part Number 926-LMC7660IMX/NOPB
U2: MCP1501-25xRW; WDFN-8-1EP_2x2mm_P0.5mm_EP0.8x1.2mm; Mouser Part Number 579-MCP1501T-25E/RW
U3: ACS711xLCTR-25AB; SOIC-8_3.9x4.9mm_P1.27mm; Mouser Part Number 250-711ELCTR25ABT
U4: OPA2727; SOIC-8_3.9x4.9mm_P1.27mm; Mouser Part Number 595-OPA2727AIDR
U5: TLA2518IRTER; QFN50P300X300X80-17N-D; Mouser Part Number 595-TLA2518IRTER
U6: DAC7811IDGST; VSSOP-10_3x3mm_P0.5mm; Mouser Part Number 595-DAC7811IDGST

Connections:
+3V3: C1.2, C6.1, C12.1, C16.1, C17.2, J3.8, L1.1, R12.1, U2.1 (VDD), U2.3 (~SHDN), U3.8 (VCC), U5.10 (DVDD), U6.8 (VDD)
+10V: C2.2, C8.2, C18.2, J3.9, Q1.3 (C), U1.8 (V+), U4.8 (V+)
-10V: C3.2, C9.1, U1.5 (VOUT), U4.4 (V-)
ADC1: U3.7 (VIOUT), U5.4 (AIN5/GPIO5)
ADC_CS: J3.6, U5.11 (~CS)
DAC_CS: J3.1, U6.6 (~SYNC)
EXT_V+: J1.1, R1.2
EXT_V-: J1.2, R3.2
GND: C1.1, C2.1, C3.1, C6.2, C7.2, C8.1, C9.2, C10.2, C11.2, C12.2, C14.2, C15.2, C16.2, C17.1, C18.1, C19.2, C20.2, H1.1, H2.1, H3.1, H4.1, J2.2, J3.10, NTC1.2, R5.1, R7.1, R11.2, Rs1.2, Rs2.2, Rs3.2, Rs4.2, Rs5.2, U1.3 (GND), U2.2 (GND), U2.4 (GND), U2.5 (GND), U2.6 (GND), U2.9, U3.5 (GND), U4.5 (+), U5.6 (AIN7/GPIO7), U5.9 (GND), U5.15 (AIN0/GPIO0), U5.16 (AIN1/GPIO1), U5.17 (EP), U6.2 (IOUT2), U6.3 (GND)
INT_V+: F1.1, R4.2, R6.1, U3.1 (IP+), U3.2 (IP+)
NTC: C20.1, R13.2, U5.5 (AIN6/GPIO6)
unnamed: C14.1, R6.2
unnamed: F1.2, J2.1
unnamed: C19.1, NTC1.1, R12.2, R13.1
unnamed: C13.2, Q1.1 (B), U4.1
unnamed: Q1.2 (E), R9.1, R11.1
unnamed: Q2.1 (D), U3.3 (IP-), U3.4 (IP-)
unnamed: Q2.2 (G), R9.2
unnamed: Q2.3 (S), R10.2, Rs1.1, Rs2.1, Rs3.1, Rs4.1, Rs5.1
unnamed: C4.2, U1.2 (CAP+)
unnamed: C4.1, U1.4 (CAP-)
unnamed: R7.2, U4.3 (+)
unnamed: C13.1, R8.2, R10.1, U4.2 (-)
unnamed: U4.6 (-), U6.1 (IOUT1)
unnamed: C5.1, R1.1, R2.1, U5.1 (AIN2/GPIO2)
unnamed: C5.2, R2.2, R3.1, U5.2 (AIN3/GPIO3)
unnamed: C7.1, R4.1, R5.2, U5.3 (AIN4/GPIO4)
unnamed: C11.1, L1.2, U5.7 (AVDD)
unnamed: C10.1, U5.8 (DECAP)
unnamed: R8.1, U4.7, U6.10 (RFB)
SPI_CIPO: J3.5, U5.12 (SDO), U6.7 (SDO)
SPI_CLK: J3.3, U5.13 (SCLK), U6.4 (SCLK)
SPI_COPI: J3.4, U5.14 (SDI), U6.5 (SDIN)
VREF: C15.1, U2.7 (OUT), U2.8 (FB), U6.9 (VREF)

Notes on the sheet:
MOSFET gate control loop
4wire connection
negative supply charge pump
MCU connector
OP AMP supply
DAC
Board Power Supply
NTC, heatsink temperature sensor
Rs 1-5 5x 50mOhm > 1W each > 1206 package route to the op amp as a kelvin connection
Voltage, 4w voltage, current, temperature measure ADC
ADC/DAC 2.5V voltage reference


Board: 4 copper layers, 50.0 x 50.0 mm, 56 parts (0 on the bottom side), 34 nets.

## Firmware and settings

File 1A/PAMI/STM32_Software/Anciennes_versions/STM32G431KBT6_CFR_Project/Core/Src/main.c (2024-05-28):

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
/* Includes ------------------------------------------------------------------*/
#include "main.h"
#include "adc.h"
#include "dma.h"
#include "i2c.h"
#include "usart.h"
#include "tim.h"
#include "gpio.h"

/* USER CODE BEGIN Includes */
#include "SSD1306.h"
#include "led.h"
#include "encodeur.h"
#include "button.h"
#include "ydlidar_x4.h"
#include "stepper.h"
#include "strategy.h"
/* USER CODE END Includes */

/* USER CODE BEGIN PD */
#define ANGLE_MIN 140
#define ANGLE_MAX 220
#define DISTANCE_MIN 200
/* USER CODE END PD */


/* USER CODE BEGIN PV */



SSD1306_COLOR screen_color = White;
uint8_t it_enc;
uint8_t it_lidar;
uint8_t it_time;
uint32_t time_100ms = 0;
uint32_t time_100ms_from_start = 0;
uint8_t is_started = 0;
uint8_t is_paused = 0;

uint16_t v_battery_raw;
float v_battery_float;

uint8_t debug = 0;

/* USER CODE END PV */

void SystemClock_Config(void);
/**
  * @brief  The application entry point.
  * @retval int
  */
int main(void)
{

  /* USER CODE BEGIN 1 */
	uint8_t led = 0;
	uint32_t encValue;
	float min_distance = 10000;
	int idx_angle_min_distance;
	uint8_t object_detected = 1;
  /* USER CODE END 1 */

  /* MCU Configuration--------------------------------------------------------*/

  /* Reset of all peripherals, Initializes the Flash interface and the Systick. */
  HAL_Init();

  /* Configure the system clock */
  SystemClock_Config();

  /* Initialize all configured peripherals */
  MX_GPIO_Init();
  MX_DMA_Init();
  MX_ADC1_Init();
  MX_I2C1_Init();
  MX_LPUART1_UART_Init();
  MX_USART1_UART_Init();
  MX_USART2_UART_Init();
  MX_TIM1_Init();
  MX_TIM2_Init();
  MX_TIM3_Init();
  MX_TIM7_Init();
  /* USER CODE BEGIN 2 */
	tx_Buffer_Size = snprintf((char *)vcp_Tx_Buffer, UART_TX_BUFFER_SIZE, "ENSEA CFR PAMI v0.1\r\n");
	HAL_UART_Transmit(&huart2, vcp_Tx_Buffer, tx_Buffer_Size, 10);


	// Init SCREEN OLED
	if(HAL_OK == SCREEN_SSD1306_Init(&hscreen1, &hi2c1)){
		tx_Buffer_Size = snprintf((char *)vcp_Tx_Buffer, UART_TX_BUFFER_SIZE, "Screen Init Done\r\n");
		HAL_UART_Transmit(&huart2, vcp_Tx_Buffer, tx_Buffer_Size, 10);
		SCREEN_SSD1306_Write_String(&hscreen1, "ENSEA CFR", Font_11x18, screen_color);
		hscreen1.CurrentX = 0;
		hscreen1.CurrentY = 18;
		SCREEN_SSD1306_Write_String(&hscreen1, "Code v0.1", Font_11x18, screen_color);
		SCREEN_SSD1306_Update_Screen(&hscreen1);
	}
	else{
		tx_Buffer_Size = snprintf((char *)vcp_Tx_Buffer, UART_TX_BUFFER_SIZE, "Screen Init Error\r\n");
		HAL_UART_Transmit(&huart2, vcp_Tx_Buffer, tx_Buffer_Size, 10);
	}

	// Init LIDAR
	YDLIDAR_X4_Init(&hlidar, &huart1);


	// Init Encodeur
	//	ENCODEUR_Init(&henc1, &htim1);
	//Bug de l'encodeur, une des 2 pins de réagit pas comme il faudrait... à changer ?!

	// Init Stepper
	Stepper_Init(&hstepperLeft, &htim3, TIM_CHANNEL_1, DIR_MOTOR_L_GPIO_Port, DIR_MOTOR_L_Pin, SET);
	Stepper_Init(&hstepperRight, &htim2, TIM_CHANNEL_1, DIR_MOTOR_R_GPIO_Port, DIR_MOTOR_R_Pin, RESET);

	// Init Time
	HAL_TIM_Base_Start_IT(&htim7);

	// Init Strategy
	STRATEGY_Init();




  /* USER CODE END 2 */

  /* Infinite loop */
  /* USER CODE BEGIN WHILE */
	while (1)
	{
		if(hlidar.newData){
			YDLIDAR_X4_Compute_Payload(&hlidar);
			min_distance = 10000;
			for(int idx_angle=ANGLE_MIN; idx_angle<ANGLE_MAX; idx_angle++){
				if((10 < hlidar.scan_response.distance[idx_angle]) &&
						(hlidar.scan_response.distance[idx_angle] < min_distance)){
					idx_angle_min_distance = idx_angle;
					min_distance = hlidar.scan_response.distance[idx_angle];
				}
			}
			if(min_distance < DISTANCE_MIN){
				LED_set_value(7);
				object_detected = 1;
//				Stepper_Stop(&hstepperLeft);
//				Stepper_Stop(&hstepperRight);
			}
			else{
				object_detected = 0;
				LED_set_value(0);
			}

			hlidar.newData = 0;
		}

		if(button.pushed){
			switch(button.name){
			case BTN_0:
				STRATEGY_Update();
				SCREEN_SSD1306_Print_Info(&hscreen1, time_100ms, time_100ms_from_start, v_battery_float, idx_angle_min_distance, min_distance, actual_strategy);
				// add code here
				break;
			case BTN_1:
				is_started = 1;
				// add code here
				break;
			case BTN_2:
				// add code here
				SCREEN_SSD1306_Print_Info(&hscreen1, time_100ms, time_100ms_from_start, v_battery_float, idx_angle_min_distance, min_distance, actual_strategy);
				break;
			case BTN_ENC:
				// add code here
				break;
			case START: // Tirette
				is_started = 1;
				// add code here
				break;
			default:

			}
			button.pushed = 0;
		}
		else if(it_time){ // each 100ms

			if(is_started && !is_paused){
				time_100ms_from_start++;
			}

			STRATEGY_Refresh(time_100ms_from_start, object_detected, is_started);

			// Get Voltage
			HAL_ADC_Start(&hadc1);
			HAL_ADC_PollForConversion(&hadc1, 1);
			v_battery_raw = HAL_ADC_GetValue(&hadc1);
			v_battery_float = v_battery_raw*0.0021; // 3.3/4095*25/10

//			if(time_100ms%10 == 0){
//				SCREEN_SSD1306_Print_Info(&hscreen1, time_100ms, time_100ms_from_start, v_battery_float, idx_angle_min_distance, min_distance, actual_strategy);
//			}

			it_time = 0;
		}

    /* USER CODE END WHILE */

    /* USER CODE BEGIN 3 */
	}
  /* USER CODE END 3 */
}

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
/**
  * @brief  Period elapsed callback in non blocking mode
  * @note   This function is called  when TIM6 interrupt took place, inside
  * HAL_TIM_IRQHandler(). It makes a direct call to HAL_IncTick() to increment
  * a global variable "uwTick" used as application time base.
  * @param  htim : TIM handle
  * @retval None
  */
void HAL_TIM_PeriodElapsedCallback(TIM_HandleTypeDef *htim)
{
  if (htim->Instance == TIM6) {
    HAL_IncTick();
  }
  /* USER CODE BEGIN Callback 1 */
	if (htim->Instance == TIM7) {
		time_100ms++;
		it_time = 1;
	}
  /* USER CODE END Callback 1 */
}

/**
  * @brief  This function is executed in case of error occurrence.
  * @retval None
  */
void Error_Handler(void)
{
  /* USER CODE BEGIN Error_Handler_Debug */
	HAL_UART_Transmit(&huart2, "Error_Handler\r\n", 15, 100);
	/* User can add his own implementation to report the HAL error return state */
	__disable_irq();
	while (1)
	{
	}
  /* USER CODE END Error_Handler_Debug */
}

#ifdef  USE_FULL_ASSERT
/**
  * @brief  Reports the name of the source file and the source line number
  *         where the assert_param error has occurred.
  * @param  file: pointer to the source file name
  * @param  line: assert_param error line source number
  * @retval None
  */
void assert_failed(uint8_t *file, uint32_t line)
{
  /* USER CODE BEGIN 6 */
	/* User can add his own implementation to report the file name and line number,
     ex: printf("Wrong parameters value: file %s on line %d\r\n", file, line) */
  /* USER CODE END 6 */
}
#endif /* USE_FULL_ASSERT */

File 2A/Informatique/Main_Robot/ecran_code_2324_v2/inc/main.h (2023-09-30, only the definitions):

#define LCD_B0_Pin GPIO_PIN_4
#define LCD_B0_GPIO_Port GPIOE
#define OTG_HS_OverCurrent_Pin GPIO_PIN_3
#define OTG_HS_OverCurrent_GPIO_Port GPIOE
#define QSPI_D2_Pin GPIO_PIN_2
#define QSPI_D2_GPIO_Port GPIOE
#define RMII_TXD1_Pin GPIO_PIN_14
#define RMII_TXD1_GPIO_Port GPIOG
#define FMC_NBL1_Pin GPIO_PIN_1
#define FMC_NBL1_GPIO_Port GPIOE
#define FMC_NBL0_Pin GPIO_PIN_0
#define FMC_NBL0_GPIO_Port GPIOE
#define ARDUINO_SCL_D15_Pin GPIO_PIN_8
#define ARDUINO_SCL_D15_GPIO_Port GPIOB
#define ULPI_D7_Pin GPIO_PIN_5
#define ULPI_D7_GPIO_Port GPIOB
#define ARDUINO_PWM_D3_Pin GPIO_PIN_4
#define ARDUINO_PWM_D3_GPIO_Port GPIOB
#define SWO_Pin GPIO_PIN_3
#define SWO_GPIO_Port GPIOB
#define SPDIF_RX0_Pin GPIO_PIN_7
#define SPDIF_RX0_GPIO_Port GPIOD
#define SDMMC_CK_Pin GPIO_PIN_12
#define SDMMC_CK_GPIO_Port GPIOC
#define ARDUINO_PWM_D9_Pin GPIO_PIN_15
#define ARDUINO_PWM_D9_GPIO_Port GPIOA
#define SWCLK_Pin GPIO_PIN_14
#define SWCLK_GPIO_Port GPIOA
#define SWDIO_Pin GPIO_PIN_13
#define SWDIO_GPIO_Port GPIOA
#define DCMI_D6_Pin GPIO_PIN_5
#define DCMI_D6_GPIO_Port GPIOE
#define DCMI_D7_Pin GPIO_PIN_6
#define DCMI_D7_GPIO_Port GPIOE
#define RMII_TXD0_Pin GPIO_PIN_13
#define RMII_TXD0_GPIO_Port GPIOG
#define ARDUINO_SDA_D14_Pin GPIO_PIN_9
#define ARDUINO_SDA_D14_GPIO_Port GPIOB
#define VCP_RX_Pin GPIO_PIN_7
#define VCP_RX_GPIO_Port GPIOB
#define QSPI_NCS_Pin GPIO_PIN_6
#define QSPI_NCS_GPIO_Port GPIOB
#define FMC_SDNCAS_Pin GPIO_PIN_15
#define FMC_SDNCAS_GPIO_Port GPIOG
#define RMII_TX_EN_Pin GPIO_PIN_11
#define RMII_TX_EN_GPIO_Port GPIOG
#define LCD_B1_Pin GPIO_PIN_13
#define LCD_B1_GPIO_Port GPIOJ
#define OTG_FS_VBUS_Pin GPIO_PIN_12
#define OTG_FS_VBUS_GPIO_Port GPIOJ
#define Audio_INT_Pin GPIO_PIN_6
#define Audio_INT_GPIO_Port GPIOD
#define FMC_D2_Pin GPIO_PIN_0
#define FMC_D2_GPIO_Port GPIOD
#define SDMMC_D3_Pin GPIO_PIN_11
#define SDMMC_D3_GPIO_Port GPIOC
#define SDMMC_D2_Pin GPIO_PIN_10
#define SDMMC_D2_GPIO_Port GPIOC
#define OTG_FS_P_Pin GPIO_PIN_12
#define OTG_FS_P_GPIO_Port GPIOA
#define NC1_Pin GPIO_PIN_8
#define NC1_GPIO_Port GPIOI
#define SAI2_MCLKA_Pin GPIO_PIN_4
#define SAI2_MCLKA_GPIO_Port GPIOI
#define LCD_DE_Pin GPIO_PIN_7
#define LCD_DE_GPIO_Port GPIOK
#define LCD_B7_Pin GPIO_PIN_6
#define LCD_B7_GPIO_Port GPIOK
#define LCD_B6_Pin GPIO_PIN_5
#define LCD_B6_GPIO_Port GPIOK
#define LCD_B4_Pin GPIO_PIN_12
#define LCD_B4_GPIO_Port GPIOG
#define SAI2_SDB_Pin GPIO_PIN_10
#define SAI2_SDB_GPIO_Port GPIOG
#define LCD_B2_Pin GPIO_PIN_14
#define LCD_B2_GPIO_Port GPIOJ
#define OTG_FS_PowerSwitchOn_Pin GPIO_PIN_5
#define OTG_FS_PowerSwitchOn_GPIO_Port GPIOD
#define DCMI_D5_Pin GPIO_PIN_3
#define DCMI_D5_GPIO_Port GPIOD
#define FMC_D3_Pin GPIO_PIN_1
#define FMC_D3_GPIO_Port GPIOD
#define ARDUINO_D7_Pin GPIO_PIN_3
#define ARDUINO_D7_GPIO_Port GPIOI
#define ARDUINO_D8_Pin GPIO_PIN_2
#define ARDUINO_D8_GPIO_Port GPIOI
#define OTG_FS_N_Pin GPIO_PIN_11
#define OTG_FS_N_GPIO_Port GPIOA
#define uSD_Detect_Pin GPIO_PIN_13
#define uSD_Detect_GPIO_Port GPIOC
#define FMC_A0_Pin GPIO_PIN_0
#define FMC_A0_GPIO_Port GPIOF
#define SAI2_SCKA_Pin GPIO_PIN_5
#define SAI2_SCKA_GPIO_Port GPIOI
#define SAI2_FSA_Pin GPIO_PIN_7
#define SAI2_FSA_GPIO_Port GPIOI
#define LCD_HSYNC_Pin GPIO_PIN_10
#define LCD_HSYNC_GPIO_Port GPIOI
#define SAI2_SDA_Pin GPIO_PIN_6
#define SAI2_SDA_GPIO_Port GPIOI
#define LCD_B5_Pin GPIO_PIN_4
#define LCD_B5_GPIO_Port GPIOK
#define LCD_BL_CTRL_Pin GPIO_PIN_3
#define LCD_BL_CTRL_GPIO_Port GPIOK
#define DCMI_VSYNC_Pin GPIO_PIN_9
#define DCMI_VSYNC_GPIO_Port GPIOG
#define LCD_B3_Pin GPIO_PIN_15
#define LCD_B3_GPIO_Port GPIOJ
#define OTG_FS_OverCurrent_Pin GPIO_PIN_4
#define OTG_FS_OverCurrent_GPIO_Port GPIOD
#define SDMMC_CMD_Pin GPIO_PIN_2
#define SDMMC_CMD_GPIO_Port GPIOD
#define TP3_Pin GPIO_PIN_15
#define TP3_GPIO_Port GPIOH
#define ARDUINO_SCK_D13_Pin GPIO_PIN_1
#define ARDUINO_SCK_D13_GPIO_Port GPIOI
#define OTG_FS_ID_Pin GPIO_PIN_10
#define OTG_FS_ID_GPIO_Port GPIOA
#define RCC_OSC32_IN_Pin GPIO_PIN_14
#define RCC_OSC32_IN_GPIO_Port GPIOC
#define FMC_A1_Pin GPIO_PIN_1
#define FMC_A1_GPIO_Port GPIOF
#define LCD_DISP_Pin GPIO_PIN_12
#define LCD_DISP_GPIO_Port GPIOI
#define LCD_VSYNC_Pin GPIO_PIN_9
#define LCD_VSYNC_GPIO_Port GPIOI
#define DCMI_PWR_EN_Pin GPIO_PIN_13
#define DCMI_PWR_EN_GPIO_Port GPIOH
#define DCMI_D4_Pin GPIO_PIN_14
#define DCMI_D4_GPIO_Port GPIOH
#define ARDUINO_PWM_CS_D5_Pin GPIO_PIN_0
#define ARDUINO_PWM_CS_D5_GPIO_Port GPIOI
#define VCP_TX_Pin GPIO_PIN_9
#define VCP_TX_GPIO_Port GPIOA
#define RCC_OSC32_OUT_Pin GPIO_PIN_15
#define RCC_OSC32_OUT_GPIO_Port GPIOC
#define LCD_G6_Pin GPIO_PIN_1
#define LCD_G6_GPIO_Port GPIOK
#define LCD_G7_Pin GPIO_PIN_2
#define LCD_G7_GPIO_Port GPIOK
#define ARDUINO_PWM_D10_Pin GPIO_PIN_8
#define ARDUINO_PWM_D10_GPIO_Port GPIOA
#define OSC_25M_Pin GPIO_PIN_0
#define OSC_25M_GPIO_Port GPIOH
#define FMC_A2_Pin GPIO_PIN_2
#define FMC_A2_GPIO_Port GPIOF
#define LCD_INT_Pin GPIO_PIN_13
#define LCD_INT_GPIO_Port GPIOI
#define LCD_R0_Pin GPIO_PIN_15
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

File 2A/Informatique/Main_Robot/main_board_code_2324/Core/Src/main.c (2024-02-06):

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
/* Includes ------------------------------------------------------------------*/
#include "main.h"
#include "dma.h"
#include "tim.h"
#include "usart.h"
#include "gpio.h"

/* USER CODE BEGIN Includes */
#include "config.h"
#include "propulsion.h"
#include "odometry.h"
#include "robot.h"
#include "bezier.h"
#include "strategy.h"
#include "serial.h"
#include "lidar.h"
#include "avoidance.h"
#include "symetry.h"
#include "control.h"
#include <stdio.h>
#include <math.h>

extern Robot robot;
/* USER CODE END Includes */


void SystemClock_Config(void);
/* USER CODE BEGIN 0 */

int _write(int file, char *ptr, int len) {
	int DataIdx;

	for (DataIdx = 0; DataIdx < len; DataIdx++) {
		HAL_UART_Transmit(&huart2, (uint8_t *) ptr++, 1, HAL_MAX_DELAY);
	}
	return len;
}

/* USER CODE END 0 */

/**
  * @brief  The application entry point.
  * @retval int
  */
int main(void)
{
  /* MCU Configuration--------------------------------------------------------*/

  /* Reset of all peripherals, Initializes the Flash interface and the Systick. */
  HAL_Init();

  /* Configure the system clock */
  SystemClock_Config();

  /* Initialize all configured peripherals */
  MX_GPIO_Init();
  MX_DMA_Init();
  MX_TIM1_Init();
  MX_TIM8_Init();
  MX_TIM11_Init();
  MX_TIM3_Init();
  MX_TIM7_Init();
  MX_TIM2_Init();
  MX_TIM6_Init();
  MX_TIM4_Init();
  MX_USART2_UART_Init();
  MX_TIM5_Init();
  MX_USART6_UART_Init();
  MX_UART4_Init();
  MX_UART5_Init();
  MX_USART1_UART_Init();
  /* USER CODE BEGIN 2 */
  HAL_TIM_Base_Start(&htim1);
  HAL_TIM_Base_Start(&htim3);
  HAL_TIM_Base_Start_IT(&htim5);

  HAL_UART_Receive_IT(&huart6, pData, 1);
  printf("Initializing propulsion system...");
  propulsion_initialize();
  propulsion_disableMotors();
  avoidance_initialize();
  HAL_Delay(200);
  printf(" Done.\r\n");

  //HAL_GPIO_TogglePin(GREEN_LED_GPIO_Port, GREEN_LED_Pin);
  //printf("Initializing strategy...");
  Strategy* strategy;
  int curveIndex = 0;
  int onSiteActionIndex = 0;
  int onMoveActionIndex = 0;

  robot.waitingForOnSiteAction = false;
  robot.waitingForOnMoveAction = false;
  robot.team = YELLOW;
  float t = 0;

  HAL_Delay(200);
  printf(" Done.\r\n");

  //HAL_GPIO_TogglePin(GREEN_LED_GPIO_Port, GREEN_LED_Pin);
  printf("Initializing lidar...");
  lidar_initialize();
  HAL_Delay(200);
  printf(" Done.\r\n");

  bool waitingForMatchStart = true;

  printf("Waiting for start...\r\n");
  pData[0] = 'o';
  int a = 0;
  while ((waitingForMatchStart == true)) {
  	  waitingForMatchStart = HAL_GPIO_ReadPin(START_GPIO_Port, START_Pin);
  	  if(wifiDataRX==0x84){
  		  waitingForMatchStart=0;
  		  strategy = strategy_initialize(7);
  		  //WifiUartTXActivation();
  	  }
  	  else if((pData[0] >= '0' && pData[0] <= '9')  && a == 0)
  	  {
  		  a = 1;
  	  	  switch(pData[0])
  	      	{
  	  	  	case '0':
  	  	  		printf("Initializing strategy...0");
  	  	  		strategy = strategy_initialize(0);
  	  	  		switchTeam(strategy);
  	       	    break;
  	      	case '1':
  	      		printf("Initializing strategy...1");
  	      		strategy = strategy_initialize(1);

  	            break;
  	      	case '2':
  	      		printf("Initializing strategy...2");
  	      		strategy = strategy_initialize(2);
  	      		switchTeam(strategy);
  	      		break;
  	        case '3':
  	        	printf("Initializing strategy...3");
  	        	strategy = strategy_initialize(3);

  	        	break;
  	        case '4':
  	        	printf("Initializing strategy...4");
  	        	strategy = strategy_initialize(4);
  	        	switchTeam(strategy);
  	        	break;
  	        case '5':
  	        	printf("Initializing strategy...5");
  	        	strategy = strategy_initialize(5);
  	            break;
  	        default:
  	            break;
  	      	}
  	  }
  }
  propulsion_enableMotors();

  printf("Initializing odometry...");
  Vector2 start = strategy->path[0]->p1;
  Vector2 startTangent = strategy->path[0]->p2;
  float startAngle = vector2_angle(vector2_diff(startTangent, start));
  odometry_setPosition(start.x, start.y);
  odometry_setAngle(startAngle);
  robot.measuredSpeed = 0;
  odometry_startKalman();
  HAL_Delay(200);
  printf(" Done.\r\n");

  printf("Go!\r\n");

  //odometry_setPosition(0, 0);
  //odometry_setAngle(0);

  HAL_UART_Receive_DMA(&huart4, &lidarBuf[0], 3);//HAL_UART_Receive_IT(&huart4, &lidarData, 1);
  HAL_UART_Receive_IT(&huart6, &armData, 1);
  /* USER CODE END 2 */

  /* Infinite loop */
  /* USER CODE BEGIN WHILE */

  /*while (1) {
	  for (int i=0; i<16; i++) {
		  printf("%d ", i);
		  printf("(%d) ", lidar_timeSinceData[i]);
	  }
	  printf("\r\n");

	  if (!lidar_frontIsClear()) {
		  printf("Front stop!\r\n");
	  }
	  if (!lidar_backIsClear()) {
		  printf("Back stop!\r\n");
	  }

	  HAL_Delay(100);
  }*/

  while (onSiteActionIndex < strategy->onSiteActionsLengths[0]) {
	  uint8_t action = strategy->onSiteActions[0][onSiteActionIndex];
	  serial_send(&action, 1, 6);
	  robot.waitingForOnSiteAction = true;

	  printf("Waiting for 0xFF...\r\n");
	  printf("%d\r\n", robot.waitingForOnSiteAction);
	  while (robot.waitingForOnSiteAction) {}
	  printf("%d\r\n", robot.waitingForOnSiteAction);
	  onSiteActionIndex++;
  }

  printf("About to move...\r\n");

  while (1) {
	  if (onMoveActionIndex < strategy->onMoveActionsLengths[curveIndex]
              && !robot.waitingForOnMoveAction
			  && !robot.waitingForOnSiteAction) {
		  uint8_t action = strategy->onMoveActions[curveIndex][onMoveActionIndex];
		  serial_send(&action, 1, 6);
		  robot.waitingForOnMoveAction = true;
	  }

	  avoidance_update(t, strategy->directions[curveIndex]);

	  if (avoidanceState == PATH_CLEAR && curveIndex < strategy->length) {
		  t = propulsion_followBezier(
				  strategy->path[curveIndex],
				  strategy->directions[curveIndex],
				  strategy->speeds[curveIndex],
				  strategy->speeds[curveIndex+1],
				  false
		  );
	  } else if (avoidanceState == PATH_OBSTRUCTED) {
		  propulsion_setSpeeds(0, 0, 0);
	  } else if (avoidanceState == BACKTRACKING) {
		  strategy->path[curveIndex] = avoidance_path(robot.position.x, robot.position.y); //Test redéfinition de trajectoire

		  t = propulsion_followBezier(
				  strategy->path[curveIndex],
				  strategy->directions[curveIndex],
				  strategy->speeds[curveIndex],
				  strategy->speeds[curveIndex+1],
				  true
		  );
	  }

	  else if (avoidanceState == BACKTRACKING2) {
	  		  strategy->path[curveIndex] = avoidance_path_return(robot.position.x, robot.position.y); //Test redéfinition de trajectoire n°2

	  		  t = propulsion_followBezier(
	  				  strategy->path[curveIndex],
	  				  strategy->directions[curveIndex],
	  				  strategy->speeds[curveIndex],
	  				  strategy->speeds[curveIndex+1],
	  				  true
	  		  );
	  	  }
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

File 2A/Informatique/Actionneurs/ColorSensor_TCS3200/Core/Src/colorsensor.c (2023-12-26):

/**
  ******************************************************************************
  * @file           : colorsensor.c
  * @brief          : Functions for the color sensor TCS3200
  * @author         : Ousmane THIONGANE
  ******************************************************************************
  */

#include "colorsensor.h"

extern TIM_HandleTypeDef htim2;

#define NUM_MEASUREMENTS 100

//Allows turning on or off the lighting LEDs
void ledToggle(int state){
	HAL_GPIO_WritePin(GPIOA, GPIO_PIN_10, state);
}

//Frequency dividers mode to control output frequency power
void frequencyScaling(int mode) {
    switch (mode) {
        case 0: //Power down
            HAL_GPIO_WritePin(GPIOB, GPIO_PIN_4, GPIO_PIN_RESET);
            HAL_GPIO_WritePin(GPIOB, GPIO_PIN_5, GPIO_PIN_RESET);
            break;

        case 1: //2% Power
            HAL_GPIO_WritePin(GPIOB, GPIO_PIN_4, GPIO_PIN_RESET);
            HAL_GPIO_WritePin(GPIOB, GPIO_PIN_5, GPIO_PIN_SET);
            break;

        case 2: //20% Power
            HAL_GPIO_WritePin(GPIOB, GPIO_PIN_4, GPIO_PIN_SET);
            HAL_GPIO_WritePin(GPIOB, GPIO_PIN_5, GPIO_PIN_RESET);
            break;

        case 3: //100% Power
            HAL_GPIO_WritePin(GPIOB, GPIO_PIN_4, GPIO_PIN_SET);
            HAL_GPIO_WritePin(GPIOB, GPIO_PIN_5, GPIO_PIN_SET);
            break;

        default:
            break;
    }
}

//FIlter color selection
void photodiodeType(int color) {
    switch (color) {
        case 0: //Clear (no filter)
        	HAL_GPIO_WritePin(GPIOB, GPIO_PIN_10, GPIO_PIN_RESET);
        	HAL_GPIO_WritePin(GPIOA, GPIO_PIN_8, GPIO_PIN_SET);
            break;

        case 1: //Red filter
        	HAL_GPIO_WritePin(GPIOB, GPIO_PIN_10, GPIO_PIN_RESET);
        	HAL_GPIO_WritePin(GPIOA, GPIO_PIN_8, GPIO_PIN_RESET);
            break;

        case 2: //Green filter
        	HAL_GPIO_WritePin(GPIOB, GPIO_PIN_10, GPIO_PIN_SET);
        	HAL_GPIO_WritePin(GPIOA, GPIO_PIN_8, GPIO_PIN_SET);
            break;

        case 3: //Blue filter
        	HAL_GPIO_WritePin(GPIOB, GPIO_PIN_10, GPIO_PIN_SET);
        	HAL_GPIO_WritePin(GPIOA, GPIO_PIN_8, GPIO_PIN_RESET);
            break;

        default:
            break;
    }
}

//Reading the duration of a rising edge
//Increasing the variable NUM_MEASUREMENTS allows averaging over multiple rising edges
int readColorValue(void) {
    uint32_t totalCounter = 0;

    for (int i = 0; i < NUM_MEASUREMENTS; ++i) {
        __HAL_TIM_SET_COUNTER(&htim2, 0);

        while (HAL_GPIO_ReadPin(GPIOA, GPIO_PIN_9) == GPIO_PIN_RESET){}
        HAL_TIM_Base_Start(&htim2);
        while (HAL_GPIO_ReadPin(GPIOA, GPIO_PIN_9) == GPIO_PIN_SET){}
        HAL_TIM_Base_Stop(&htim2);

        totalCounter += __HAL_TIM_GET_COUNTER(&htim2);
    }

    int averageCounter = totalCounter / NUM_MEASUREMENTS;

    return averageCounter;
}

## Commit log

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2023-10-01 Mise à jour
    [Carte_Routage.kicad_pcb, Carte_Routage.kicad_sch]
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2023-10-06 ajout fichier dimensionnement
    [Dimensionnement_mécanique_projet-2A.xlsx]
2023-10-06 add lidar projet
    [LIDAR_Ares_v1_3 Debug.cfg]
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2023-10-16 Ajout de la CAO de la base du robot
    [base_robot.f3d]
2023-10-16 ajout dernière version CAO base robot
    [Partie_Haute_Plastique v10.3mf, Partie_Haute_Plastique.f3z, base_robot.f3d]
2023-10-19 added electronic load kicad project
    [DAC7811IDGST.stp, TLA2518IRTER.stp, load.kicad_pcb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]
2023-10-26 added gerber files
    [load-B_Cu.gbl, load-B_Mask.gbs, load-B_Paste.gbp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]
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2023-11-07 ajout stl
    [base.stl, bras_droit.stl, bras_gauche.stl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]
2023-11-12 création de la CAO de plusieurs pièces du robot et assemblage du robot en entier
    [Base_Robot.f3d, Partie_Haute_Plastique v10.3mf, Partie_Haute_Plastique.f3z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]
2023-11-12 ajout datasheet et schema elec
    [ALIMENTATION.kicad_sch, Intelligence.kicad_sch, MainBoard.kicad_pcb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]
2023-11-14 add stl
    [vis panneaux.stl]
2023-11-14 add support batterie
    [support batterie.stl]
2023-11-14 impression 3d
    [oddo part 1.1.stl, oddo part2.2.stl, oddo part2.stl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]
2023-11-16 ajout équairestl
    [equaire.stl]
2023-11-16 schematic and pcb update, added BOM
    [ALIMENTATION.kicad_sch, Intelligence.kicad_sch, MainBoard.kicad_pcb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]
2023-11-16 removed duplicated project, updated schematic and pcb, added BOM
    [PCB.kicad_pcb, PCB.kicad_sch, PSU.kicad_sch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]
2023-11-16 added vias to pcb
    [MainBoard.kicad_pcb]
2023-11-20 ajout de pièce suplémentaire pour impression
    [dessus.stl, jupe_ar_droite.stl, jupe_arrire_gauche.stl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]
2023-11-23 add cao and stl file
    [ACOPLE EJE 8 mm a 5 mm.stl, dessuspince.stl]
2023-11-23 add piece
    [Nema17_25mm v1 v1.f3d, dessuspince.stl]
2023-11-24 modif stl pince diametre servo moteur 5 mm to 4.4mm
    [bas_equerre.stl, bras_droit.stl, bras_gauche.stl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]
2023-11-27 fichiers CAO
    [bord de soutien v47.stl]
2023-11-27 ajout des CAO
    [bord de soutien v28.stl, bord de soutien v29.3mf, support_nemma_stockage v4.stl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]
2023-12-01 new stl
    [Corps_ascenseur.stl, pousse pot.stl, rabat pot 2.stl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]
2023-12-05 add stl for stockage
    [contour_stokcage.stl]
2023-12-05 Ajout PCB kicad ugway
    [puissance_pcb.kicad_pcb, puissance_pcb.kicad_sch]
2023-12-19 ajout fichiers CAO créés
    [Assemblage_Pince_V2 v46.stl, Base_V2 v84.stl, puissance_pcb.kicad_sch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]
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2024-01-16 add motor
    [XL-320.step]
2024-01-16 PCB de puissance
    [puissance.kicad_pcb, puissance.kicad_sch]
2024-01-23 update pcb
    [GPIO_filtering.kicad_sch, LT1076.kicad_sch, puissance.kicad_sch]
2024-01-23 fix kicad bug
    [puissance.kicad_sch]
2024-01-23 pcb puissance
    [Connecteurs.kicad_sch, GPIO_filtering.kicad_sch, GPIOfiltering.kicad_sch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]
2024-01-24 update schematic
    [GPIO_filtering.kicad_sch, UART_Connector.kicad_sch, XL320.kicad_sch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]
2024-01-24 pcb puissance update
    [GPIO_3V3_Connector.kicad_sch, GPIO_filtering.kicad_sch, XL320.kicad_sch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]
2024-01-24 suppression diode et changement des feuille hiérarchique
    [Connectors.kicad_sch, GPIO_3V3_Connector.kicad_sch, GPIO_filtering.kicad_sch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]
2024-01-24 add datasheet info
    [Connectors.kicad_sch]
2024-01-24 update schematic add testpoint and level shifter
    [XL320.kicad_sch, puissanceok.kicad_sch]
2024-01-25 debut assignation empreintes
    [GPIO_3V3_Connector.kicad_sch, GPIO_filtering.kicad_sch, LT1076.kicad_sch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]
2024-01-26 update pcd
    [GPIO_filtering.kicad_sch, LT1076.kicad_sch, UART_Connector.kicad_sch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]
2024-01-26 add schematic update and footprint
    [LT1076.kicad_sch, XL320.kicad_sch, puissanceok.kicad_sch]
2024-01-26 finalize schematic + footprints
    [GPIO_filtering.kicad_sch, LT1076.kicad_sch, UART_Connector.kicad_sch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]
2024-01-26 version 1 placement composants
    [puissanceok.kicad_pcb]
2024-01-26 trie des composants, placement des composants
    [puissanceok.kicad_pcb]
2024-01-26 update puissance
    [GPIO_filtering.kicad_sch, LT1076.kicad_sch, UART_Connector.kicad_sch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]
2024-01-27 update pcb and schematic
    [2.54 mm DUPONT MALE PIN HEADER, IO, 2X20, RPi4ModelB.SLDPRT, 2.54 mm DUPONT MALE PIN HEADER, IO, 2X40, RPi4ModelB.SLDPRT, 2.54 mm DUPONT MALE PIN HEADER, POE, 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]
2024-01-28 version2 placements composants
    [puissanceok.kicad_pcb]
2024-01-28 pcb place components and add power/gnd planes
    [GPIO_filtering.kicad_sch, LT1076.kicad_sch, UART_Connector.kicad_sch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]
2024-01-29 update errors
    [puissanceok.kicad_pcb]
2024-01-29 update pcbpuissance
    [puissanceok.kicad_pcb]
2024-01-29 restore file
    [Connecteurs.kicad_sch, GPIO_3V3_Connector.kicad_sch, GPIO_filtering.kicad_sch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]
2024-01-30 add other version of pcb
    [Connecteurs.kicad_sch, GPIO_3V3_Connector.kicad_sch, GPIO_filtering.kicad_sch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]
2024-01-30 suppr redflag
    [puissanceok.kicad_pcb]
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2024-02-05 Avoidance strategy 2nd path
    [main.c]
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2024-02-08 add first schematic PAMI
    [PAMI_mb.kicad_pcb, PAMI_mb.kicad_sch, TMC2225.kicad_sch]
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2024-02-16 code for YDLIDAR_X4 stm32 ok
    [puissanceok-B_Cu.gbr, puissanceok-B_Mask.gbr, puissanceok-B_Paste.gbr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]
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2024-03-27 pcb PAMI fix bugs
    [GPIO_Filter.kicad_sch, PAMI_mb.kicad_pcb, PAMI_mb.kicad_sch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]
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2024-03-30 add PAMI PCB Teardrops, export gerbers
    [GPIO_Filter.kicad_sch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]
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2024-05-24 Correction gestion fichiers
    [GPIO_Filter.kicad_sch, PAMI_mb.kicad_sch, Stepper_Driver_TMC2225-SA-T.kicad_pcb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]
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

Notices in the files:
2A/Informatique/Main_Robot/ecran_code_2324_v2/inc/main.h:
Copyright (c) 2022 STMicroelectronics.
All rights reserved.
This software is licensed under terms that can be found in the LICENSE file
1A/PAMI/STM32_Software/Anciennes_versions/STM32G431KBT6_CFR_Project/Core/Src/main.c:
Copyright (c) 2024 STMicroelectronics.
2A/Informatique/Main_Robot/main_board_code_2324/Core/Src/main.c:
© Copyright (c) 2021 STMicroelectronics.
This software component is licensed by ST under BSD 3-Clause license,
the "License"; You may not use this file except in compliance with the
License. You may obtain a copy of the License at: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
